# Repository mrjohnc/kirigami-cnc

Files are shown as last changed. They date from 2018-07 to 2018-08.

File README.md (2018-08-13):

# kirigami-cnc
A CNC machine to mark, cut and crease paper

It is based around the design principles of: 

* All materials as accessible as possible to make it as easy to build and improve the design as possible
* Strong enough to allow the cutting of many materials
* To be easy to construct
* To be affordable

The project is inspired by the work of Sam Calisch at MIT
https://www.youtube.com/watch?v=JtKi8lNSqvw

The current design is largely inspired by Maslow CNC, an open source CNC router with a design similar to a hanging plotter. 
https://github.com/MaslowCNC

The board on which the machine moves is angled so that gravity pushes the cutting tool into the material being cut.

## Current status
### Done
A very basic first version has been created moves but has no toolchain (click image for video). There is one toolhead for a craft knife which cuts paper. The motion system is very wobbly because the way the bearings run on the toolhead base is poor and need to be redesigned.

(http://www.youtube.com/watch?v=BQzhzq3MdRw "First Kirigami CNC test moves")

### Biggest issues
#### Hardware
* Find a better way to attach belt to ring with less wobbliness
* Replace plastic bearings with real bearings on motor plate
* Find way for machine to understand its position
* More tools
* Find way to raise and lower tools
* Find way to add more weight to the toolhead so it can cut consistently
* Some way to create a board that can operate at 45% so it can apply enough force to cut properly

#### Software
* Everything

## Building a Kirigami CNC
#### Printed parts
Printed parts are available in the STLs folder. Print each file the number of times shown, files were printed successfully in PLA using an 0.4mm nozzle with 20% infill and 1.2mm top, bottom and sides.

* **1x** Base 
* **2x** Counterweight cylinder top 
* **2x** Counterweight cylinder 
* **2x** Counterweight lid
* **2x** Counterweight 
* **16x** Fixer 
* **2x** Large wheel inner
* **4x** Large wheel outer 
* **2x** Motor bracket
* **1x** Motor stencil
* **2x** Ring bearing holder part 1
* **2x** Ring bearing holder part 2
* **4x** Ring spacer
* **1x** Ring 
* **6x** Small wheel inner
* **12x** Small wheel outer 
* **1x** Tool bearing holder
* **1x** Tool blade holder 
* **8x** Wheel spacer

#### Non printed parts
* **1x** Snap off utility knife blade
* **2x** NEMA 17 motors
* **2x** GT2 belts
* **2x** GT2 belt gears
* **3x** 608 bearings
* **1x** 3D printer control board
* **1x** Power supply
* **1x** 3D printer thermister
* **1kg/2lbs** Table salt (used in counterwiegh)
* **6x** Cable ties
* **1x** M3 square nut
* **5x10mm** M3 bolts
* **8x10mm** M3 bolts
* **9x18mm** M3 bolts
* **12x35mm** M3 bolts
* **1x** Large sheet of ply wood or similar stiff material

#### Software
(A first version, likely to change)
* Slic3r
* Pronterface

### Construction
#### Motor mount
<p align="left">
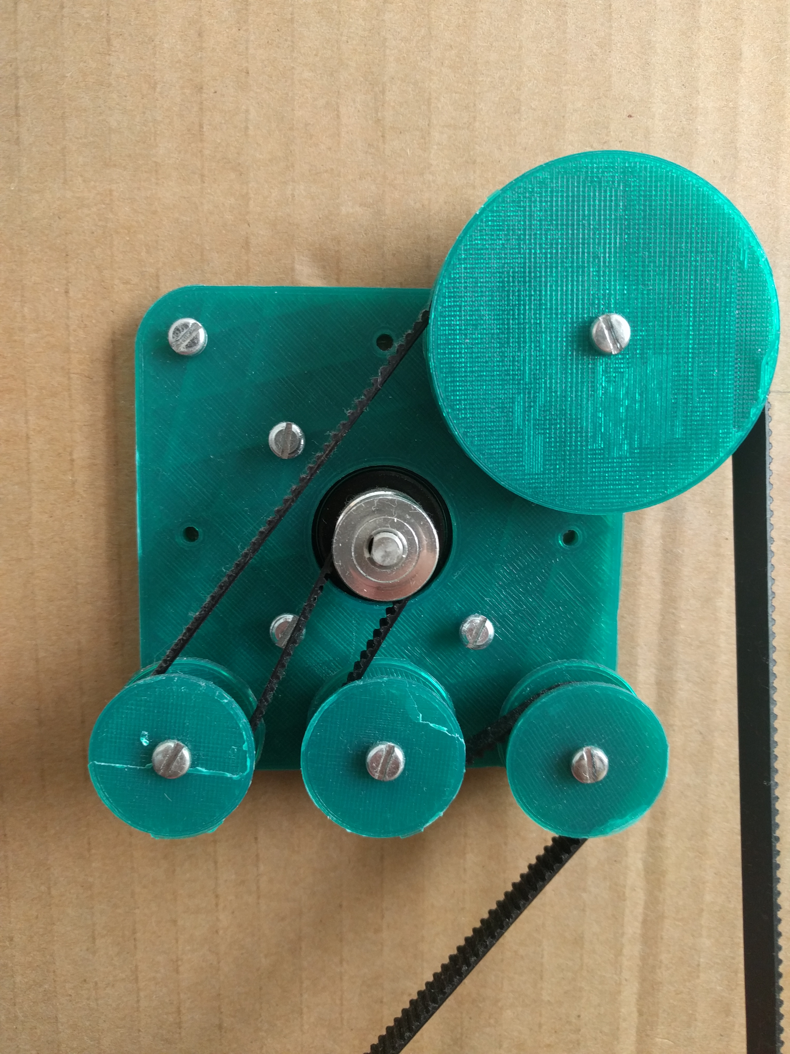
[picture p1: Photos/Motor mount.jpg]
  
</p>
Printed parts:
* **8x** Fixer 
* **2x** Large wheel inner
* **4x** Large wheel outer 
* **2x** Motor bracket
* **1x** Motor stencil
* **6x** Small wheel inner
* **12x** Small wheel outer 
* **8x** Wheel spacer

Non printed parts:
* **4x10mm** M3 bolts (bolt motors into plate)
* **8x35mm** M3 bolts (for outside corners where a printed bearing is used)
* **1x18mm** M3 bolt (for top corner opposite large gear)
* **1x** Large sheet of ply wood or similar stiff material
* **1x** GT2 belt
* **2x** NEMA 17 motors

1. Use the **Motor stencil** draw the shapes in the top left and right **ply wood** to cut, the outer edge of the stencil should be at least 10 cm from the side edges of the material to allow for space for the counterwight to go up and down.
2. Cut out the shape of the motor and drill the holes for the bolts, using a 3mm drill will allow the screws to bite into the material as well as being attached using the fixers.
3. Screw the motor to the Motor bracket using the 10mm bolts
4. Create each of the plastic bearings for the GT2 belt using a **Small wheel inner** placed between two **Small wheel outer**s and screw a 35mm bolt through till it reaches the top of the bolt.
5. Screw a **Wheel spacer** onto the back of the plastic bearing you've just made
6. Screw the bolt with the parts on into one of the positions shown above, attaching it to the plywood board.
7. Repeat for the other small wheels and the big wheel, making sure the big wheel is on the outside edge of the board.

#### Base
<p align="left">
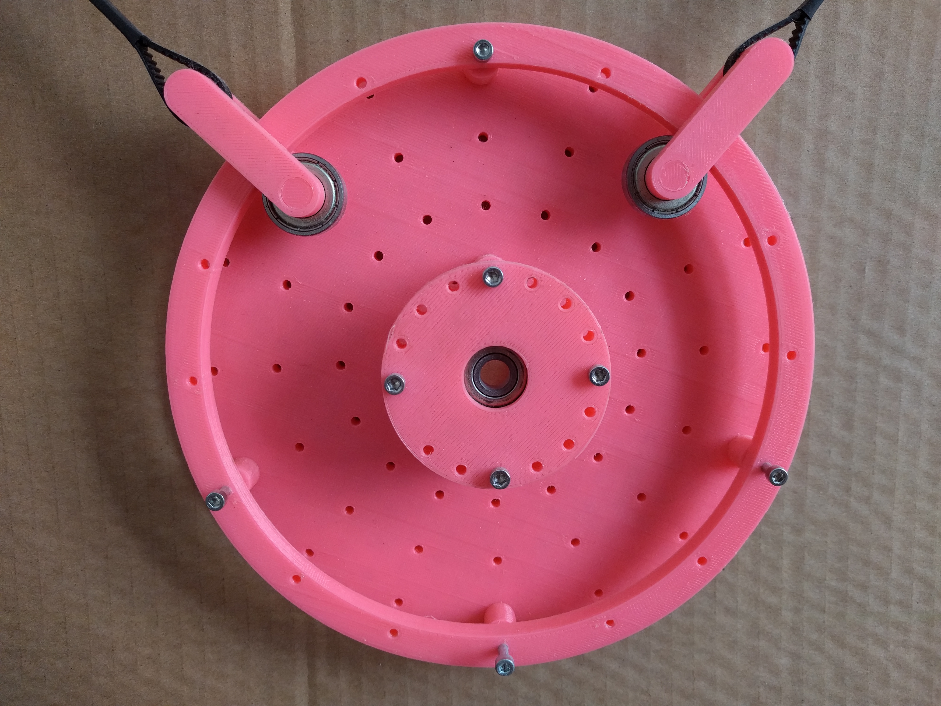
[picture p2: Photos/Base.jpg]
  
</p>
Printed parts:
* **1x** Base 
* **2x** Ring bearing holder part 1
* **2x** Ring bearing holder part 2
* **4x** Ring spacer
* **1x** Ring 

Non printed parts
* **4x18mm** M3 bolts (outside ring)
* **4x35mm** M3 bolts (inside ring) 
* **3x608** bearing

#### Cutting head
<p align="left">
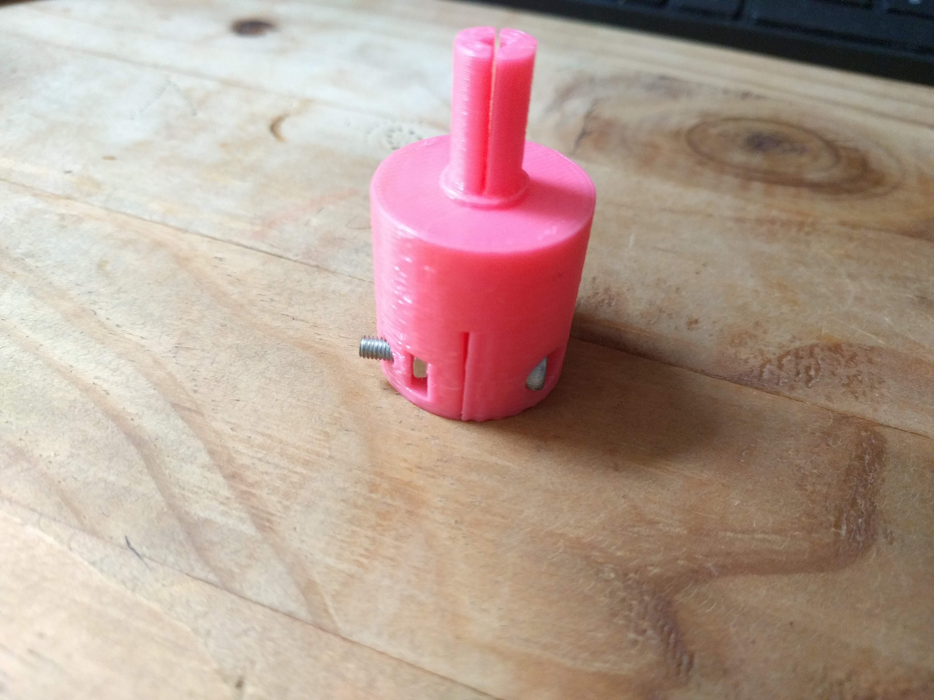
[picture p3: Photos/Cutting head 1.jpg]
  
</p>
<p align="left">
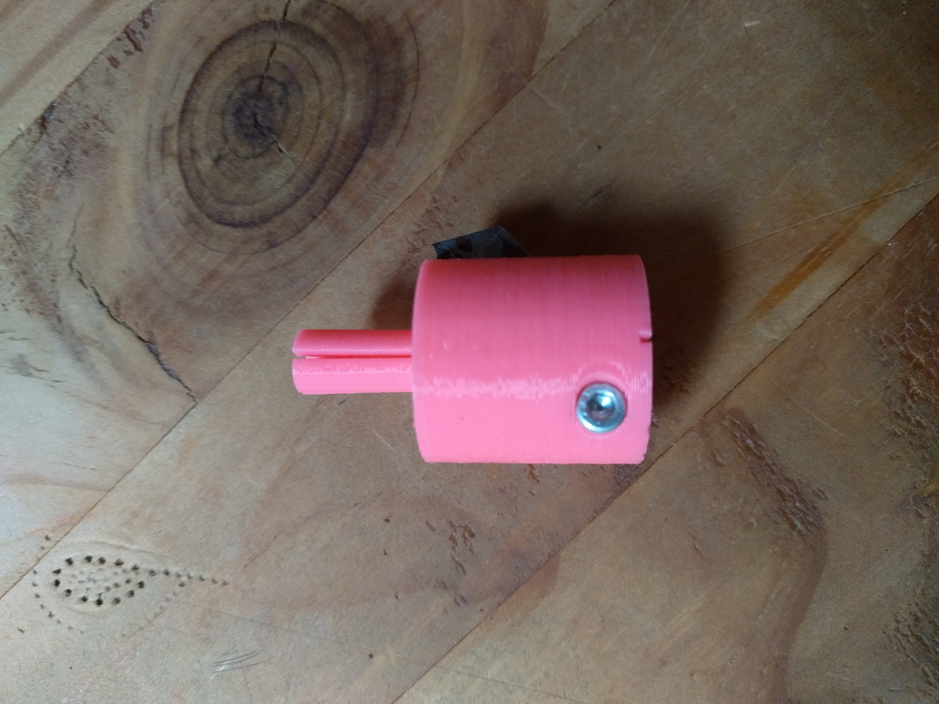
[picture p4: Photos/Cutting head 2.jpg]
  
</p>
Printed parts
* **1x** Tool blade holder 

Non printed parts
* **1x18mm** M3 bolt
* **1x10mm** M3 bolt
* **1x** M3 square nut
* **1x** blade

1. Push the square but into the hole in the **Tool blade holder**
2. Screw the bolt into the hole on the **Tool blade holder** that is the opposite side to the nut, so the bolt goes throught the middle, don't tighten it.
3. Snap two section off the blade
4. Slide the snapped off blades in to the slot in the **Tool blade holder** so that it is poking out the bottom the depth of the material you want to cut, make sure the edge of the blade lines up with the line on the bottom. BE CAREFUL NOT TO CUT YOURSELF
5. Tighten the nut so that the knife blade doesn't move.

#### Control board
<p align="left">
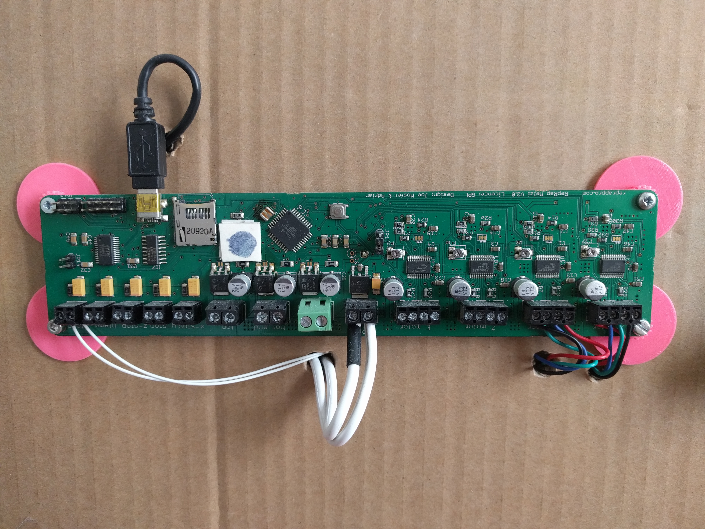
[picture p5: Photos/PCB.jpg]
  
</p>
Parts needed
* **4x??mm** M3 bolts
* **1x** 3D printer control board
* **8x** Fixer 

1. Put the control board where you want to mount it on the plywood board, between the motors away from anything moving is sensible.
2. Mark on the board using the mounting holes on the board where you will drill the mounting holes in the plywood board
3. Drill the holes
4. Slide the bolt through the board and add a fixer to the back of each bolt to create a gap between the board and the plywood.
5. Mount the board on the plywood
6. Attach on the back using the remianing 4 fixers.
7. Wire up the motors
8. Add the thermistor (the thermistor is used to not trip the mintemp sensor in Pronterface

#### Counterweight
<p align="left">
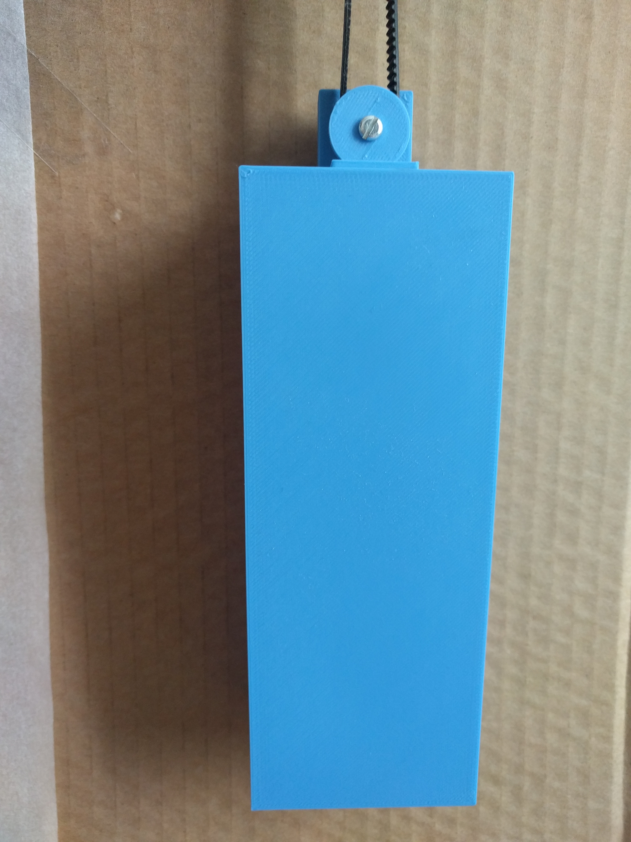
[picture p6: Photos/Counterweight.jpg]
  
</p>
Parts needed (per counterwieght)
Printed parts:

* **1x** Counterweight cylinder top 
* **1x** Counterweight cylinder 
* **1x** Counterweight lid
* **1x** Counterweight 

Non printed parts
* **2x18mm** M3 bolts
* **1kg/2lbs** Table salt

1. Fill each of the counterweights to the top with table
2. Push the **Counterweight cylinder top** intot the hole in the **Counterweight**
3. Screw the **Counterweight cylinder top** followed by the **Counterweight cylinder** onto the 18mm bolt.
4. Screw the bolt into the hole in the counterweight, this will stop the lid coming off
5. Loop the GT2 belt around the **Counterweight cylinder** teeth facing inwards so they will fit together
6. Cable tie the belt together, don't worry about excess belt, don't cut it in case you want to use a larger board in future

#### First movements
DONT MOUNT THE KNIFE TOOL FOR THIS TEST, USE A PEN IF YOU LIKE
1. Tape a large piece of paper to the plywood board
2. Put the toolhead roughly in the middle
3. Open Pronterface and connect to the control board
4. Write down the thermistor temperature
3. Load a simple shape in Slic3r that is 0.2mm thick (I used Tinkercad to make a circle)
4. Slice the shape like you're printing on a 3D printer, make the layer height 0.2mm, set the hotend temperature to a few degrees lower than the room temperature
5. Export the GCode
6. Open up the GCode in a text editor and remove the first few lines to make sure you got rid of any endstop homing commands
7. Load the file in Pronterface and press start
8. The machine should roughly make the shape

This is as far as I've got.......

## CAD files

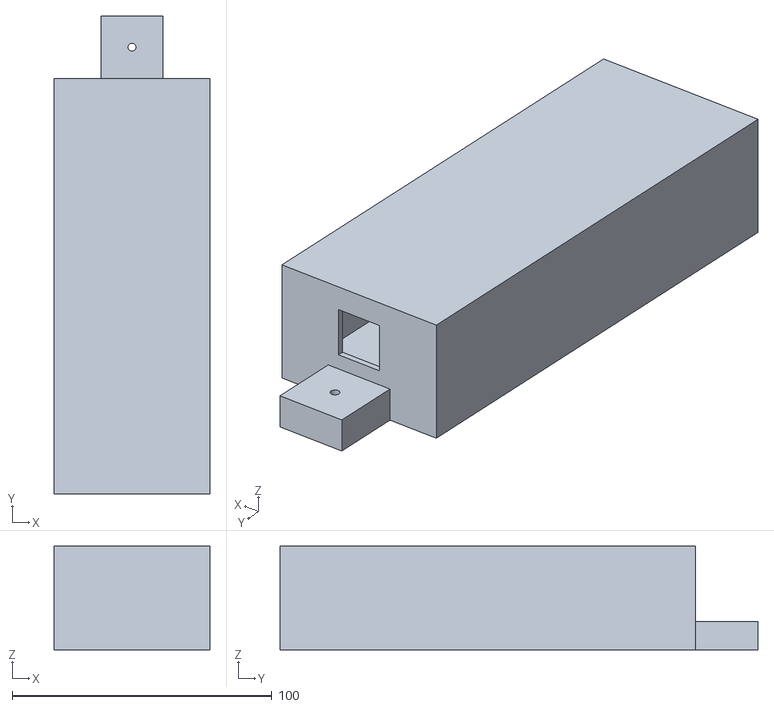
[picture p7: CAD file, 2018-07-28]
STLs/Counterweight.stl
60.0 x 184.0 x 40.0

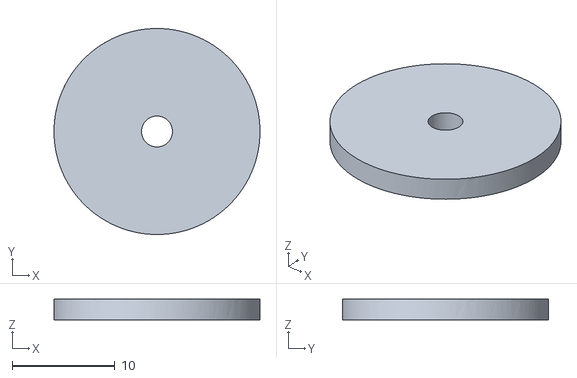
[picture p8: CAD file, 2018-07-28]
STLs/Counterweight cylinder top.stl
20.0 x 20.0 x 2.00

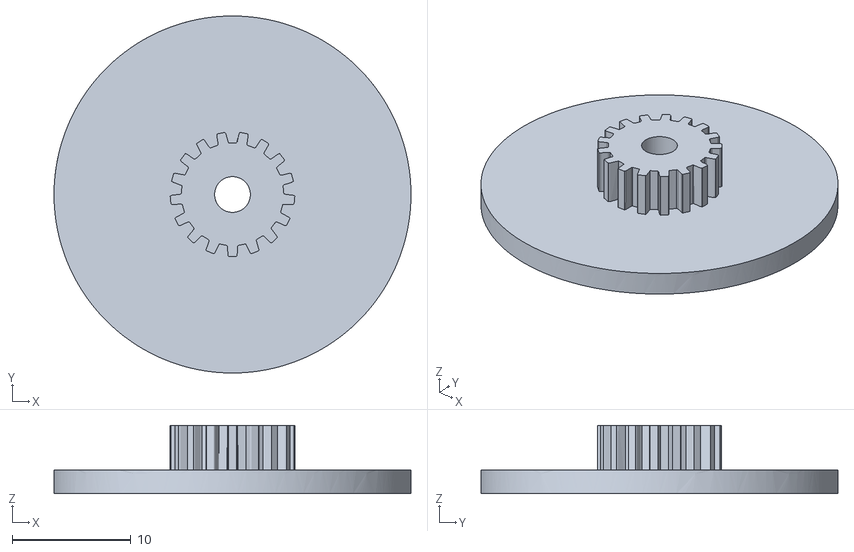
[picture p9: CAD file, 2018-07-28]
STLs/Fixer.stl
30.0 x 30.0 x 5.75

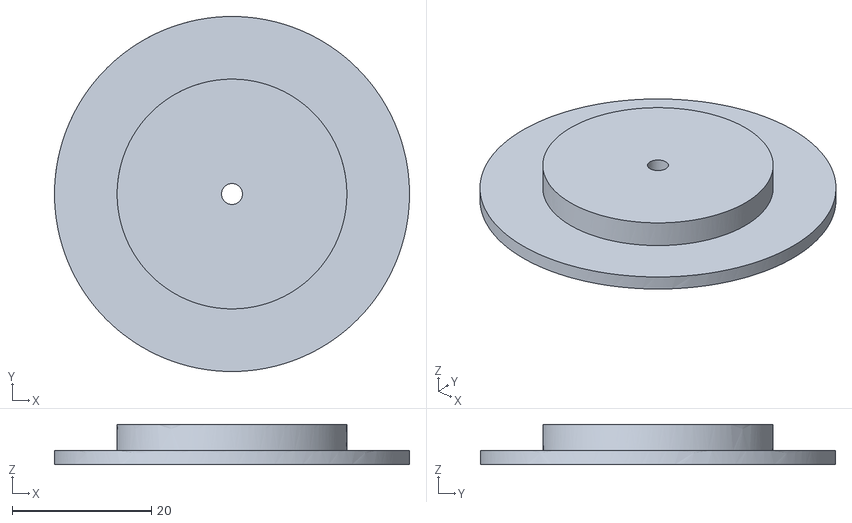
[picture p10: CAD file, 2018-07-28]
STLs/Large wheel outer.stl
51.0 x 51.0 x 5.75

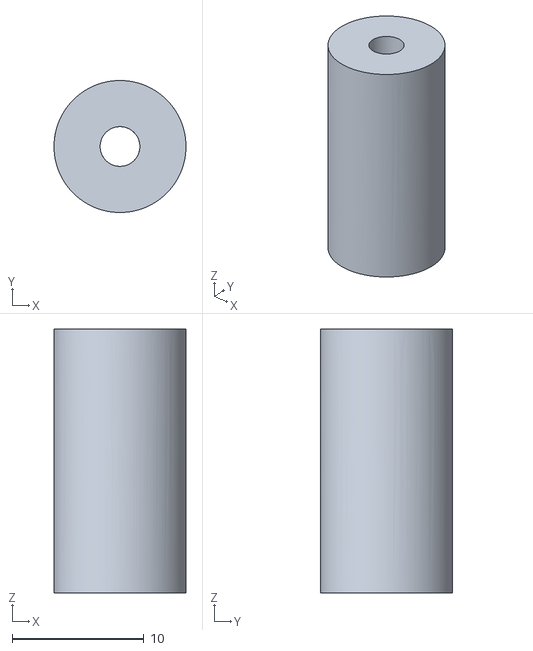
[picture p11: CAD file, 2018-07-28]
STLs/Ring spacer.stl
10.0 x 10.0 x 20.0

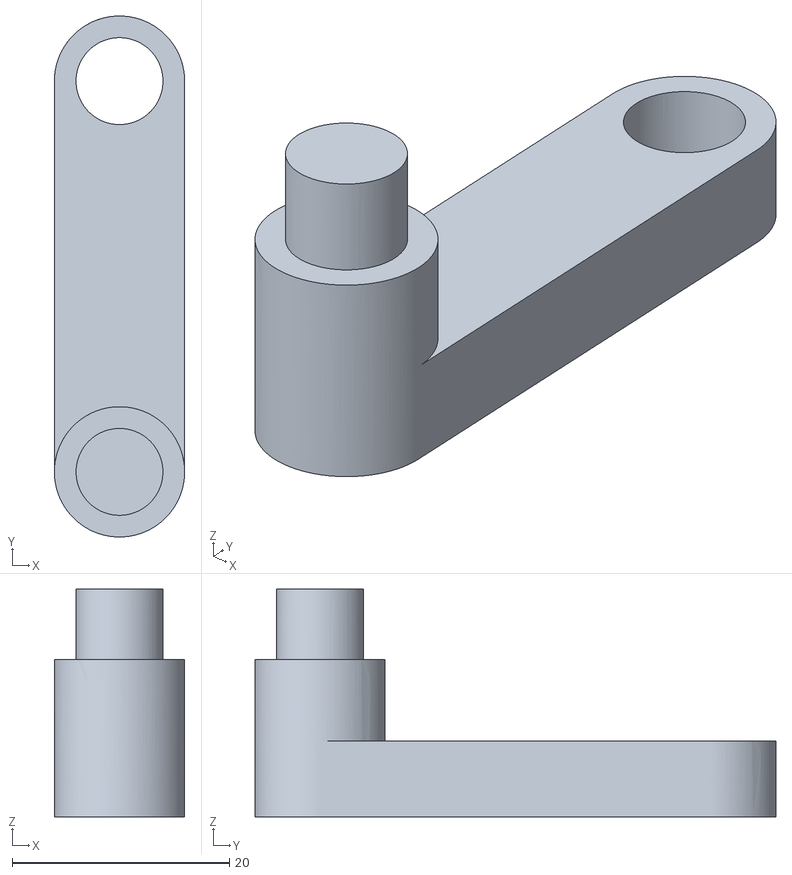
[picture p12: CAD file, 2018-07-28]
STLs/Ring bearing holder part 1.stl
12.0 x 48.0 x 21.0

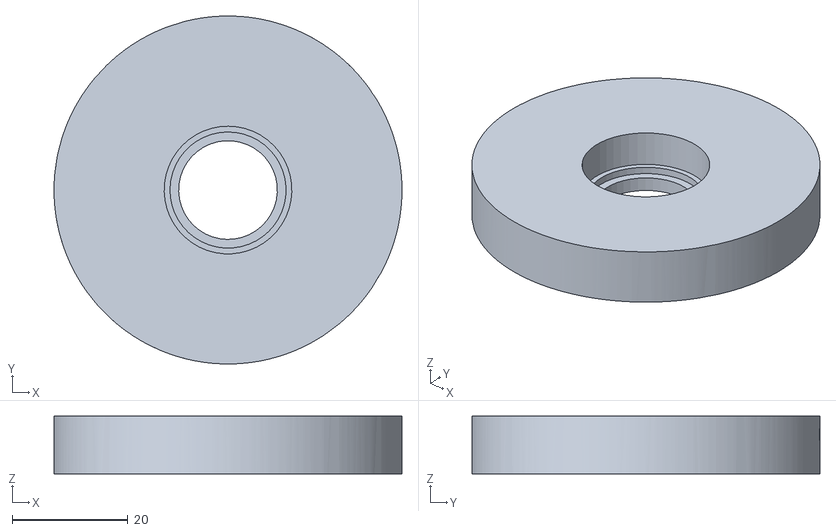
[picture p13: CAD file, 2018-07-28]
STLs/Tool bearing holder.stl
60.0 x 60.0 x 10.0

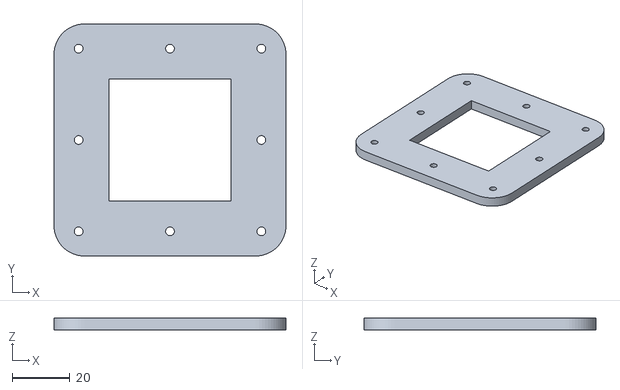
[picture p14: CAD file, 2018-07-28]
STLs/Motor stencil.stl
80.0 x 80.0 x 4.00

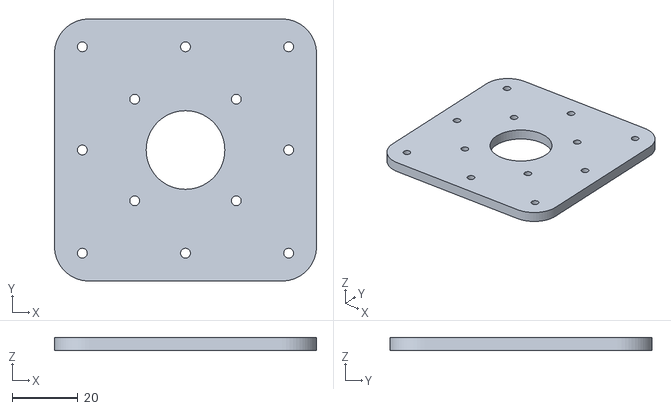
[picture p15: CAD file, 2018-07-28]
STLs/Motor bracket.stl
80.0 x 80.0 x 4.00

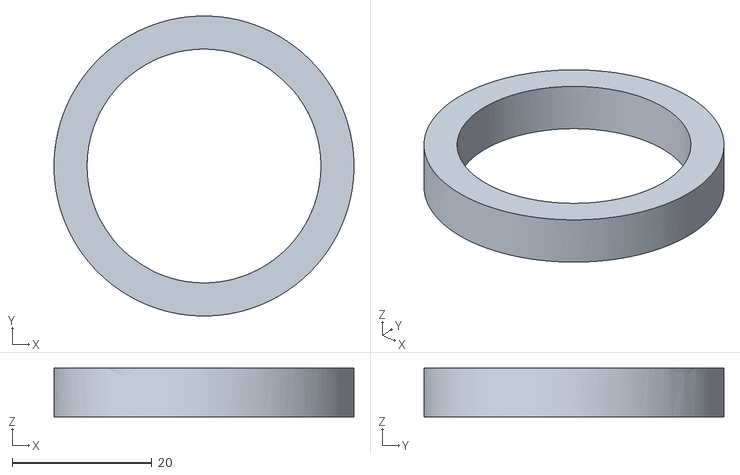
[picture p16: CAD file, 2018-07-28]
STLs/Large wheel inner.stl
43.0 x 43.0 x 7.00

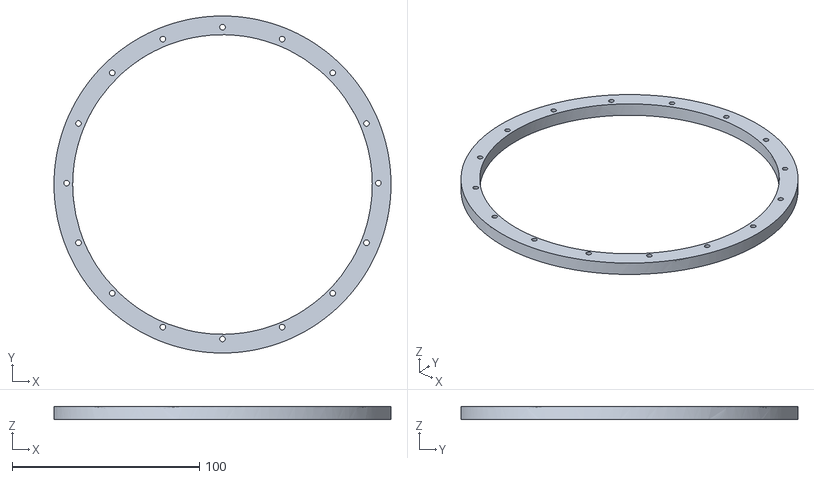
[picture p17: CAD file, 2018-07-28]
STLs/Ring.stl
180.0 x 180.0 x 7.00

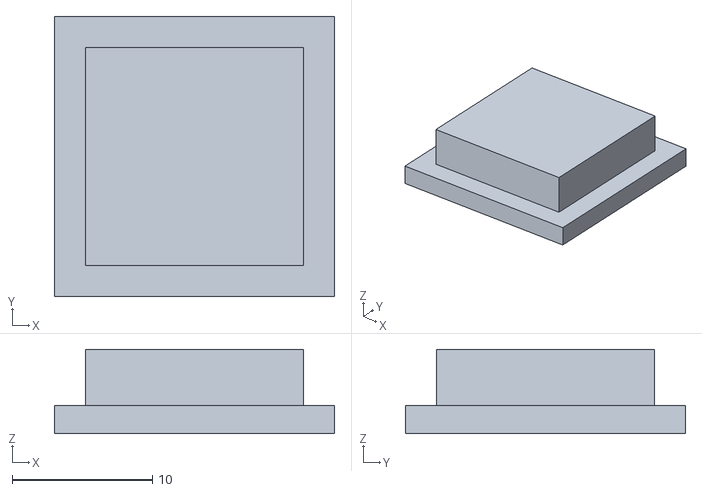
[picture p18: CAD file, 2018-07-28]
STLs/Counterweight lid.stl
20.0 x 20.0 x 6.00

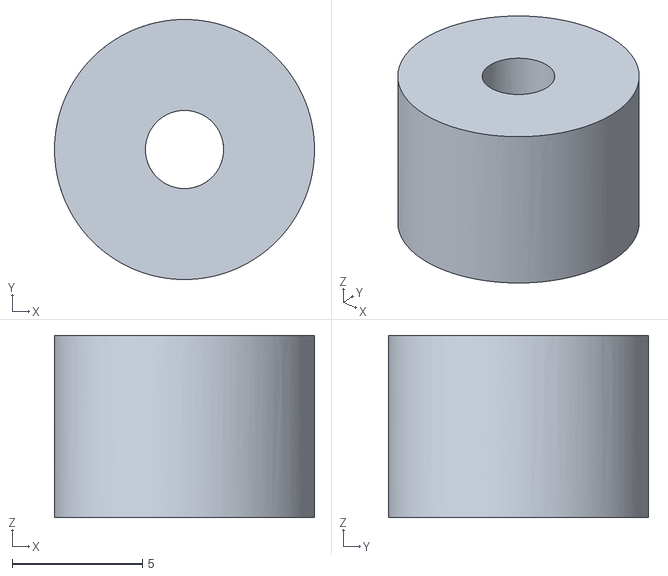
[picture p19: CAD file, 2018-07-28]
STLs/Counterweight cylinder.stl
10.0 x 10.0 x 7.00

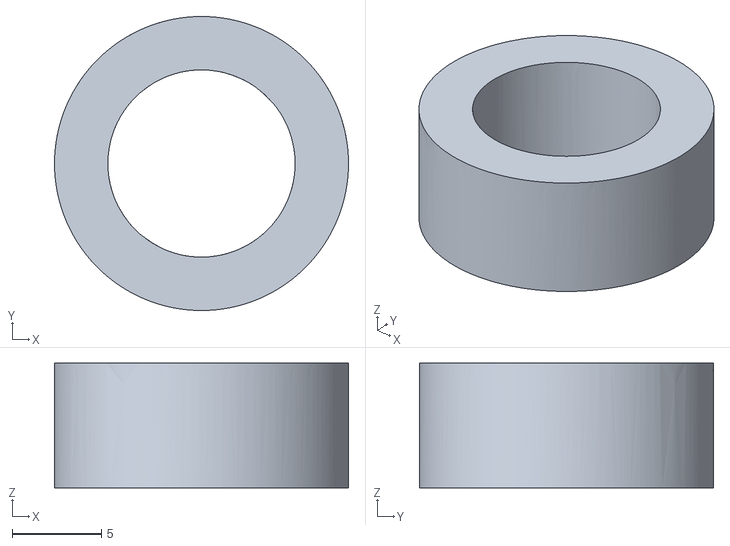
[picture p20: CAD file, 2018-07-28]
STLs/Small wheel inner.stl
16.5 x 16.5 x 7.00

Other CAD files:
STLs/Tool blade holder.stl
STLs/Small wheel outer.stl
STLs/Wheel spacer.stl
STLs/Ring bearing holder part 2.stl

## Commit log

2018-02-04 added parts
    [GT2 belt cog.stl, bearing clip part 1.stl, bearing clip part 2.stl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]
2018-02-24 added file
    spacer for electronics board
    [electronics board spacer.stl]
2018-02-24 replaced wrong part with new one
    [GT2 belt cog.stl]
